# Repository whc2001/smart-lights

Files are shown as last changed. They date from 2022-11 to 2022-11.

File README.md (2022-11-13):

# smart-lights

This is a non-intrusive light switch automation controller based on the design of [suyashkumar/smart-lights](https://github.com/suyashkumar/smart-lights). The goal is to accommodate a regular lever-type light switch into Home Assistant without replacing the original switch. ESPHome is used.

demo

# Wiring and installation

A Wemos D1 mini is used as the controller. In my case, the servo needs to be at least MG995 to have enough strength to toggle the switch (SG90 didn't work as it's too weak). The capacitor across 5V power is mandatory (the larger the better, for which I used 470uF), otherwise there is a risk of frying the onboard 3.3V LDO. You can use anything that's momentary and normally open for the manual button and end-stop switch, but you may need to modify the 3D model of the installation panel to fit your part. Use a power supply with enough current (I used a phone charger of 5V 3A, plugging into the micro USB of the D1 mini) for the servo to work.

After checking the wiring, use ESPHome utility to compile and write the code to your D1 mini. You can now test with the manual button to see if the servo is working. Install the servo onto the panel and fix the panel onto your switch. Adjust the `level` of `servo.write` inside `turn_on_action` and `turn_off_action` so that the servo could swing wide enough to toggle the switch fully, but without stalling. You may need to test this multiple times.

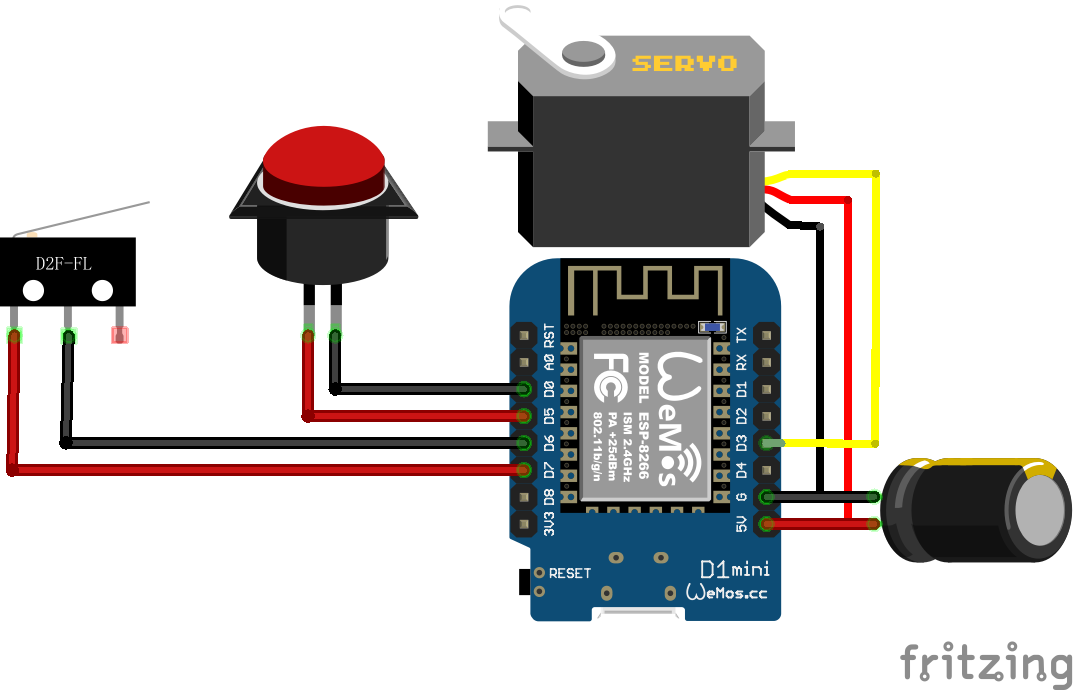
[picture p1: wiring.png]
wiring


# TODO

- [x] Refine and upload ESPHome config YAML

- [x] Add an endstop switch or similar to provide some sort of feedback

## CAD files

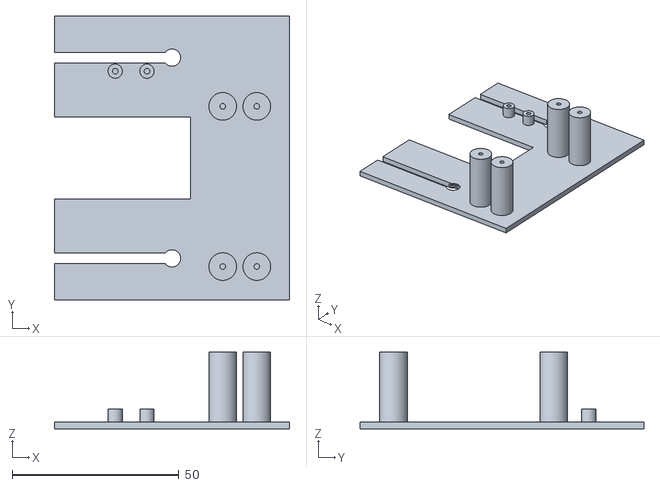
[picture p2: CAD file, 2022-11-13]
3DModels/plate.stl
70.4 x 85.0 x 23.0

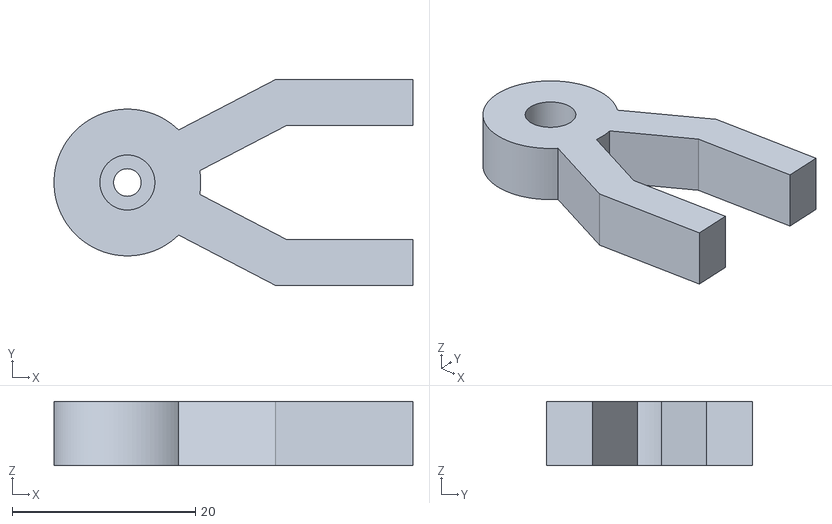
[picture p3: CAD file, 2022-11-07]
3DModels/arm.stl
39.1 x 22.4 x 7.00

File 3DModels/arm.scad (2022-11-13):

servoInnerDiameter = 6;
extensionLength = 11.0;
screwDiameter = 3;
barWidth = 5;
barAngle = 55;
armLength = 15;
componentHeight = 7;
$fn = 100;

module servoMount()
{
    difference()
    {
        cylinder(d = servoInnerDiameter + 10, h = componentHeight);
        cylinder(d = servoInnerDiameter, h = componentHeight / 1.5);
        cylinder(d = screwDiameter, h = componentHeight);
    }
}
module armBase()
{
    rotate([ 0, 0, -barAngle / 2 ]) translate([ (servoInnerDiameter + 1) / 2, -barWidth / 2, 0 ]) union()
    {
        cube([ extensionLength + 5, barWidth, componentHeight ]);
        translate([ extensionLength + 5, 0, 0 ]) rotate([ 0, 0, barAngle / 2 ])
            cube([ armLength, barWidth, componentHeight ]);
    }
}
module arms(armType = 0)
{
    union()
    {
        armBase();
        mirror([ 0, 1, 0 ]) armBase();
    }
}
module drawAll()
{
    union()
    {
        servoMount();
        arms();
    }
}
rotate([ 180, 0, 0 ]) drawAll();

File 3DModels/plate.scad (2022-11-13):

holeDia = 6.15;
baseThickness = 2;
wellDepth = baseThickness / 2;

servoStrutDia = 4.28;
servoStrutHeight = 22;
servoStrutHoleDia = 1.7;
servoStrutHoleHeight = 10;
bottomStrutOffset = 32.5;
inlineServoStrutSep = 10.21;
servoWidth = 20.4;
servoStrutsX = 5;

switchStrutsX = -17;
switchStrutsY = 26;
switchWidth = 9.5;
switchStrutsDia = 4.28;
switchStrutsHeight = 5;
switchStrutsHoleDia = 1.7;
switchStrutsHoleHeight = 5;

slotWidth = holeDia - 3;
$fn = 80;

module strut(outerDia, outerHeight, innerDia, innerHeight)
{
    difference()
    {
        cylinder(d = outerDia, h = outerHeight);
        translate([ 0, 0, outerHeight - innerHeight ]) cylinder(d = innerDia, h = innerHeight);
    }
}

module servoStruts()
{
    translate([ servoWidth + servoStrutsX, -bottomStrutOffset, 0 ])
        strut(servoStrutDia + 4, servoStrutHeight, servoStrutHoleDia, servoStrutHoleHeight);
    translate([ servoWidth + servoStrutsX - inlineServoStrutSep, -bottomStrutOffset, 0 ])
        strut(servoStrutDia + 4, servoStrutHeight, servoStrutHoleDia, servoStrutHoleHeight);
    translate([ servoWidth + servoStrutsX, -bottomStrutOffset + 43.68 + servoStrutDia, 0 ])
        strut(servoStrutDia + 4, servoStrutHeight, servoStrutHoleDia, servoStrutHoleHeight);
    translate([ servoWidth + servoStrutsX - inlineServoStrutSep, -bottomStrutOffset + 43.68 + servoStrutDia, 0 ])
        strut(servoStrutDia + 4, servoStrutHeight, servoStrutHoleDia, servoStrutHoleHeight);
}

module switchStruts()
{
    translate([ switchStrutsX, switchStrutsY, 0 ])
        strut(switchStrutsDia, switchStrutsHeight, switchStrutsHoleDia, switchStrutsHoleHeight);
    translate([ switchStrutsX + switchWidth, switchStrutsY, 0 ])
        strut(switchStrutsDia, switchStrutsHeight, switchStrutsHoleDia, switchStrutsHoleHeight);
}

module base()
{
    difference()
    {
        // Panel
        cube([ 70.36, 85, baseThickness ], center = true);

        // Switch slot
        cube([ 11, 24.5, baseThickness + 2 ], center = true);
        translate([ -17.59, 0, 0 ]) cube([ 35.18, 24.5, baseThickness + 2 ], center = true);

        // Upper hole and slot
        translate([ 0, 30.05, (baseThickness / 2 - wellDepth) ])
            cylinder(r = (holeDia + 1) / 2, h = wellDepth, center = true);
        translate([ 0, 30.05, 0 ]) cylinder(r = (holeDia - 1) / 2, h = baseThickness, center = true);
        translate([ -17.59, 30.05, 0 ]) cube([ 35.18, slotWidth, baseThickness + 2 ], center = true);

        // Lower hole and slot
        translate([ 0, -30.05, (baseThickness / 2 - wellDepth) ])
            cylinder(r = (holeDia + 1) / 2, h = wellDepth, center = true);
        translate([ 0, -30.05, 0 ]) cylinder(r = (holeDia - 1) / 2, h = baseThickness, center = true);
        translate([ -17.59, -30.05, 0 ]) cube([ 35.18, slotWidth, baseThickness + 2 ], center = true);
    }
}

module drawAll()
{
    union()
    {
        base();
        servoStruts();
        switchStruts();
    }
}

drawAll();

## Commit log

2022-11-11 Add endstop switch strut
    [plate.scad]
2022-11-13 Formatting with clang-format
    [arm.scad, plate.scad, plate.stl]
2022-11-13 Correct the model of the servo used
